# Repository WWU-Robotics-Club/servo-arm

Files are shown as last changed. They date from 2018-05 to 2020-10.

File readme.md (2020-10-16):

Servo robot arm inspired by [Pinaut's project](https://www.youtube.com/watch?v=bLnAJ-mSElE)

pot_control controls the arm via a second arm with potentiometers to measure position like in Pinaut's video.

For assembly instructions see the readme under [instructions](instructions/readme.md).

blueberry_servo_arm is made to work with "keyframes" function of [this fork](https://github.com/CalebJ2/Android-Bluetooth-Remote-Control) of the blueberry remote control app. With the app, keyframe animations can be saved on the phone and played back on the arm.

## Parts list

* Set of laser cut parts made out of 1/8 inch plywood. If that isn't an option they could be cut out of cardboard or foamboard. There are .dwg to .pdf converters that could be used to print plans if autocad isn't available.
* 1x Arduino Uno & USB cable
* 1x V5.0 Sensor Shield (or similar)
* 5x 9g servos (I used 1 SG90 and 4 MG90S servos)
* 5x WH148 Rotary Potentiometers 10K Ohm 15mm shaft
* Misc. 20mm and 10mm jumper wires to extend servo wires and connect potentiometers
* (maybe) 1x USB battery bank to power it. The servos can draw more power than some computer USB ports can supply.

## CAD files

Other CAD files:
autocad files/arm-main.dwg
autocad files/arm-grabber.dwg
autocad files/arm-control.dwg

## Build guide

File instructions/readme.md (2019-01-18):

# Assembly instructions

For glue hot glue works well.

Servo horns are the things you put on servos. Friction fit is probably enough but optionally you can screw them on or use a little hot glue. 

Center each servo before permanently connecting a servo horm. Just turn them to figure out their range and turn it to the center, or use a servo tester or receiver or something to have the servo center itself.

## Step 1

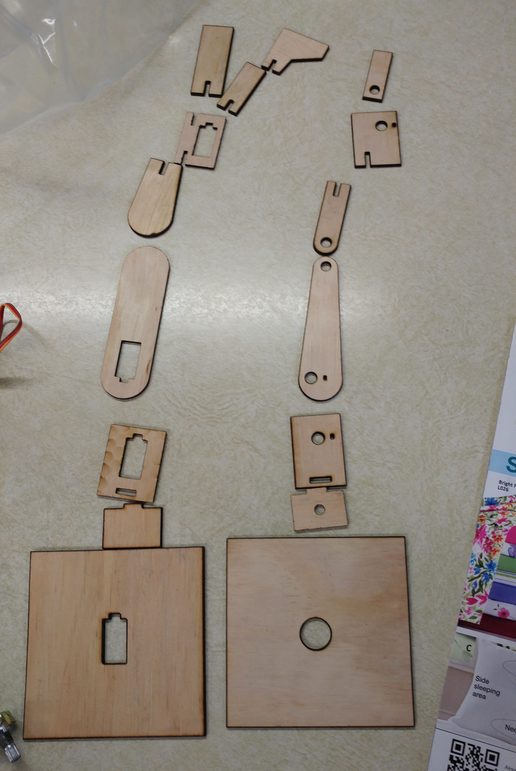
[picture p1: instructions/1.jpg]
Step 1


Take inventory. Left side is the servo arm, right is the control arm.

---

## Step 2

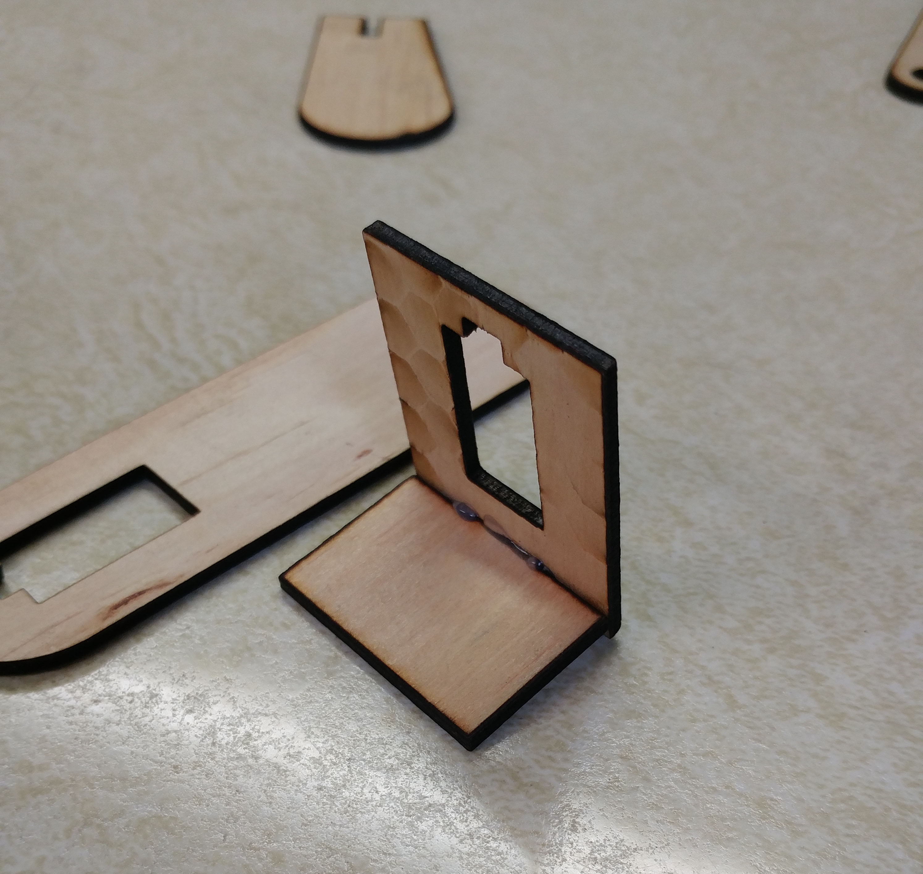
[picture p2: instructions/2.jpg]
Step 2


Servo arm first. Glue these.

---

## Step 3

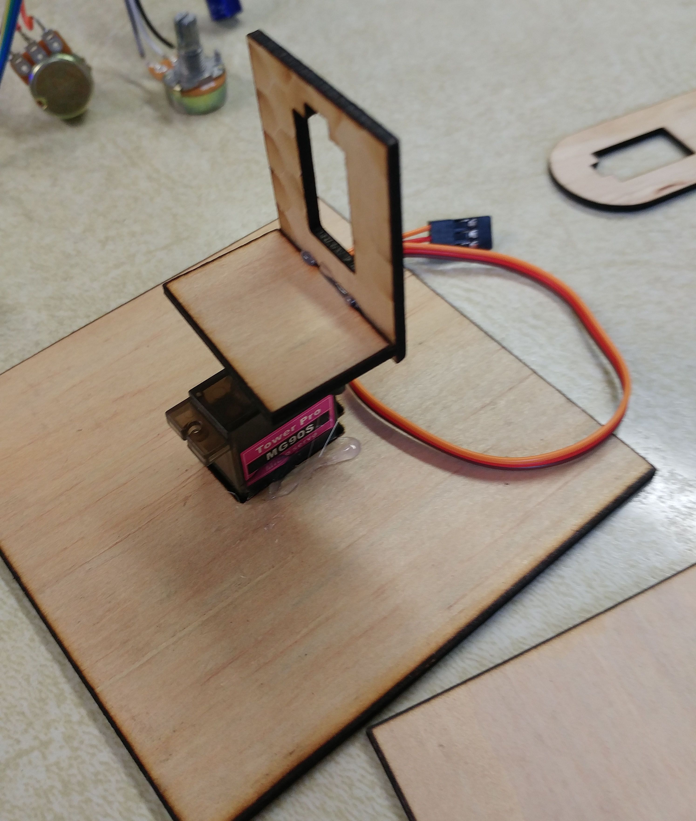
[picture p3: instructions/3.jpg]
Step 3


Glue in the base servo. Put a servo horn on the servo. Glue the part 2 part on top.

---

## Step 4

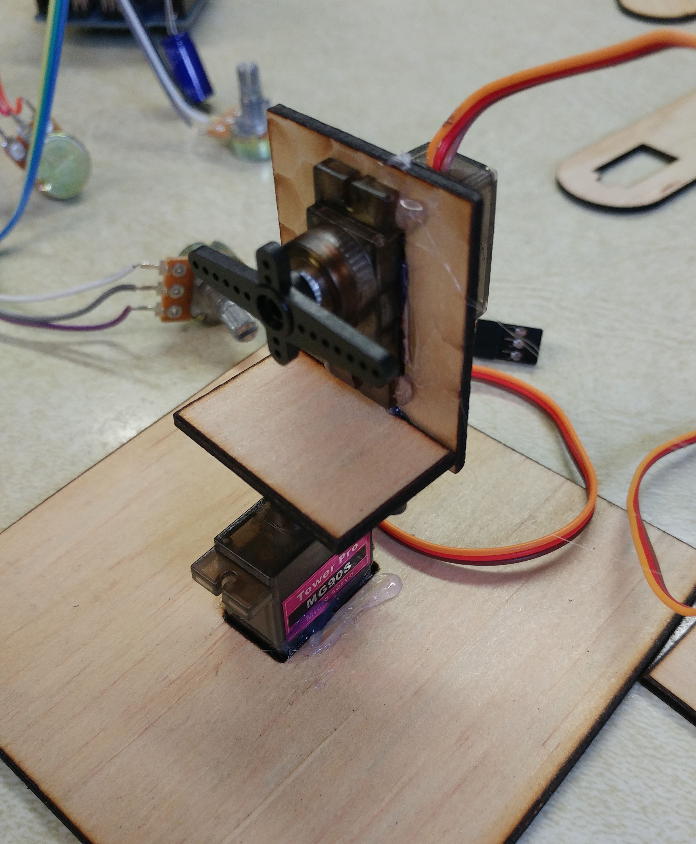
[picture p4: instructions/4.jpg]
Step 4


Glue in the elbow servo with the turning part up.

---

## Step 5

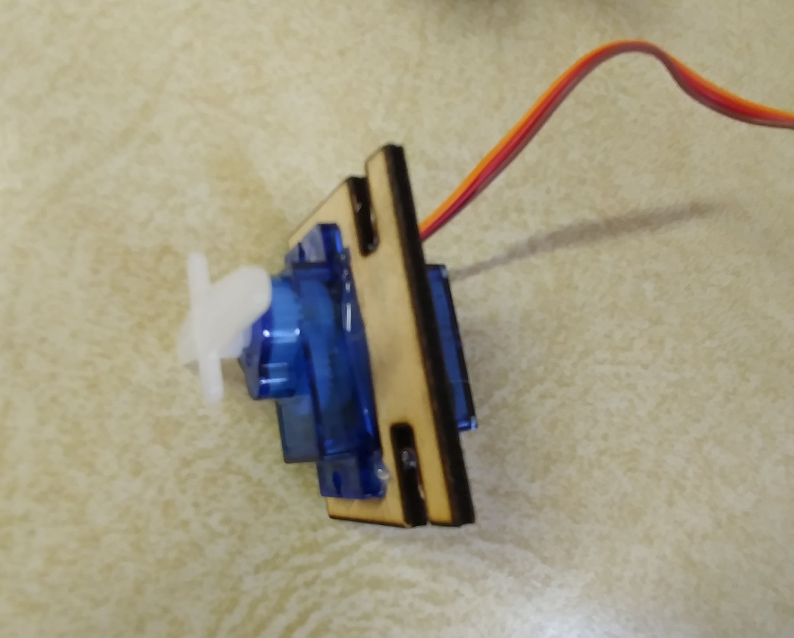
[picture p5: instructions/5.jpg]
Step 5


Carefully glue the grabber servo into the grabber servo mount with the wire facing forward and the slots on the right.

---

## Step 6

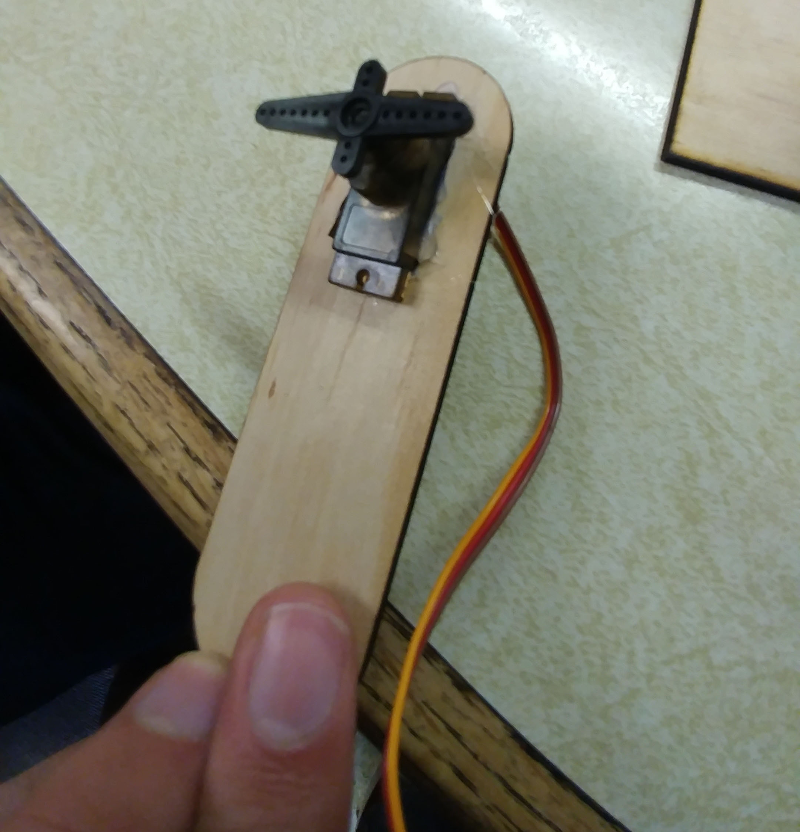
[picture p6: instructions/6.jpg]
Step 6


Glue in the wrist servo with the turning part towards the end.

---

## Step 7

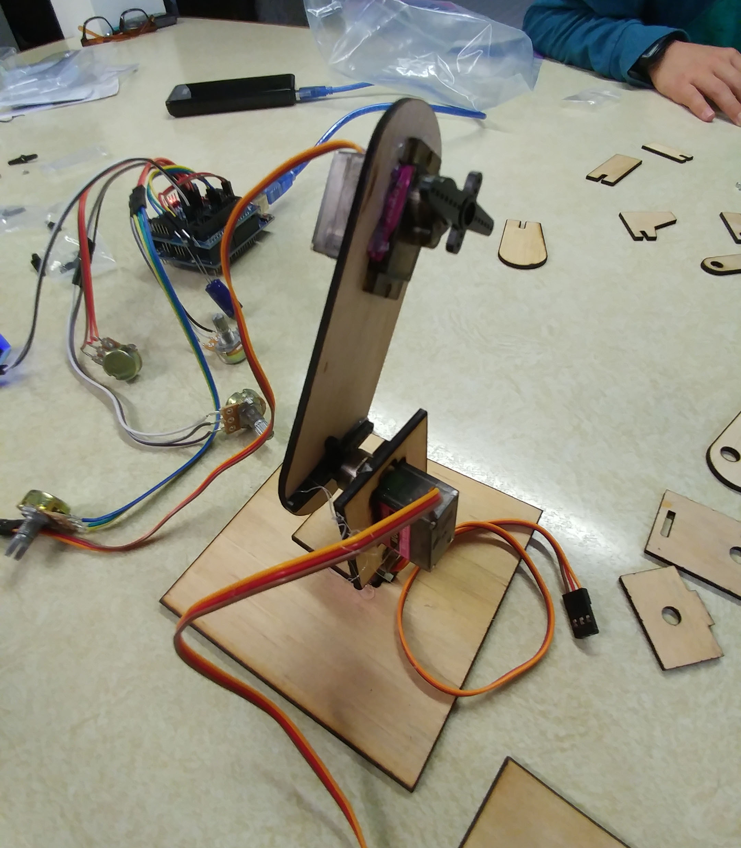
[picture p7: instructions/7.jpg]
Step 7


Glue the arm part onto the elbow servo.

---

## Step 8

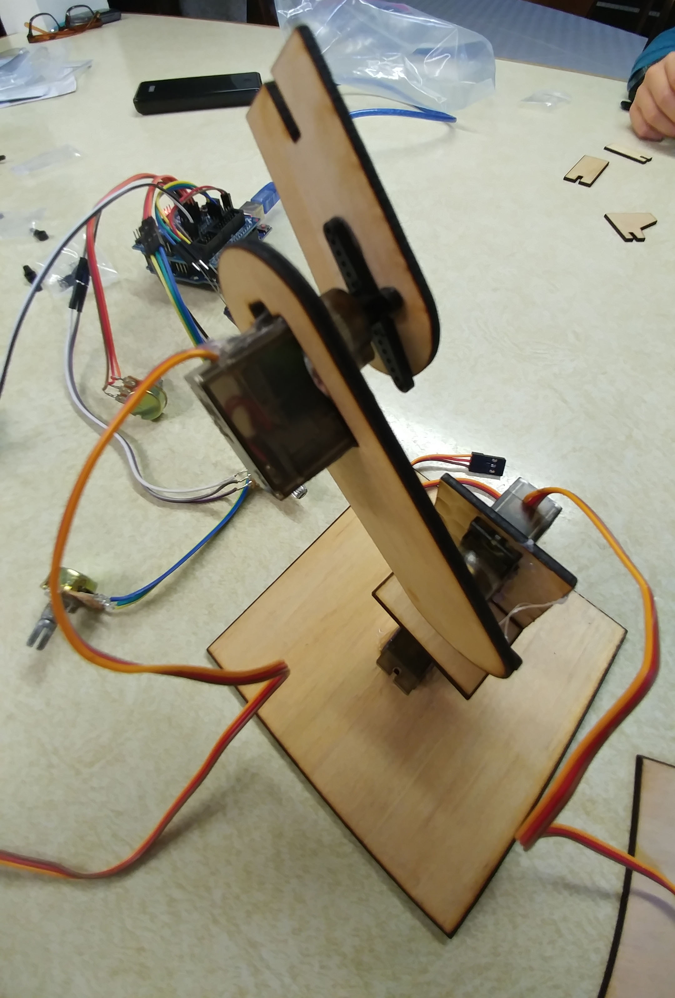
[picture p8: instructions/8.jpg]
Step 8


Glue the first wrist part onto the wrist servo with the 90deg corner on top and the slightly wider angle corner on the bottom.

---

## Step 9

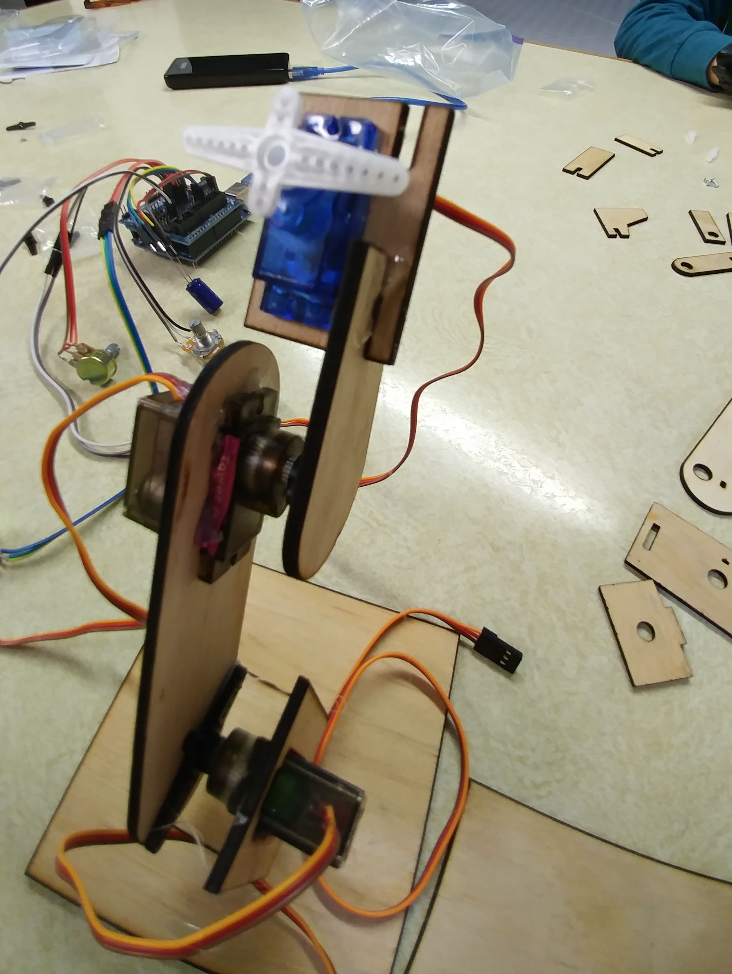
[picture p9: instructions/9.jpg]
Step 9


Slide the grabber servo mount onto the first wrist part. Glue if needed.

---

## Step 10

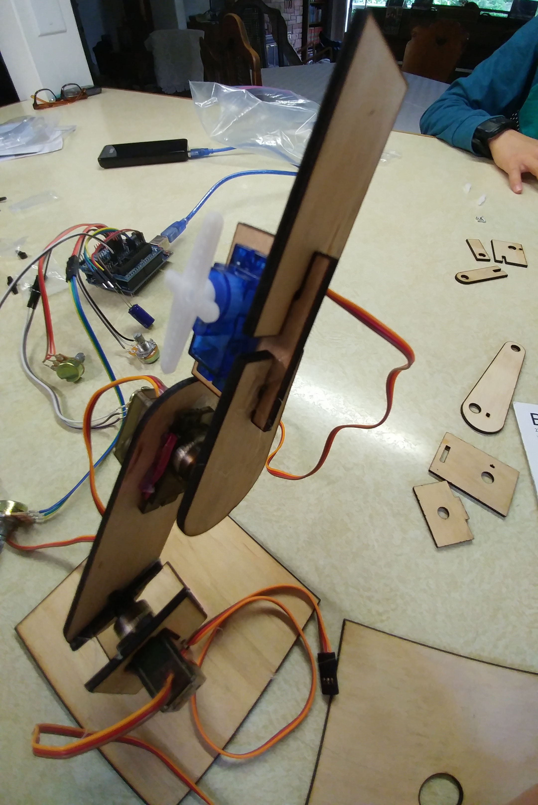
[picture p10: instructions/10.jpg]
Step 10


Slide the grabber "hand" onto the grabber servo holder.

---

## Step 11

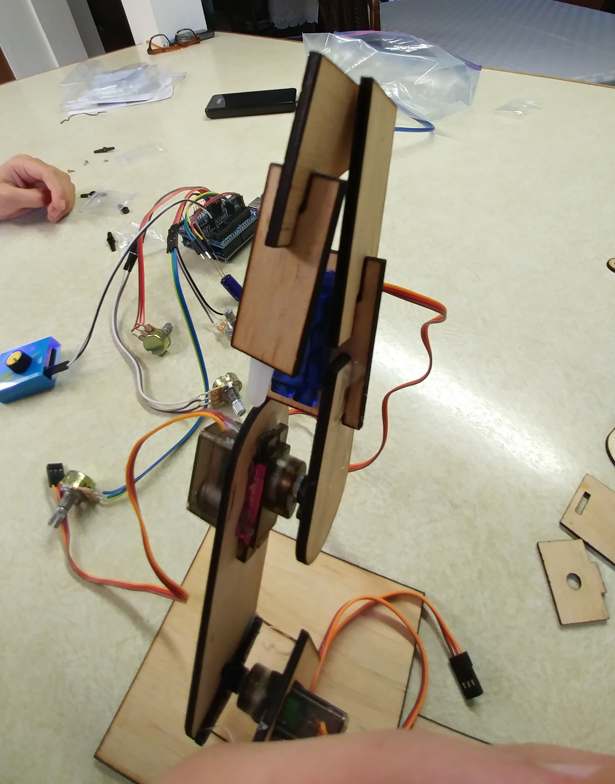
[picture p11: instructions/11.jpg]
Step 11


Slide together the grabber "thumb" pieces and glue them onto the grabber servo. Made sure the end of the hand and thumb line up.

---

## Step 12

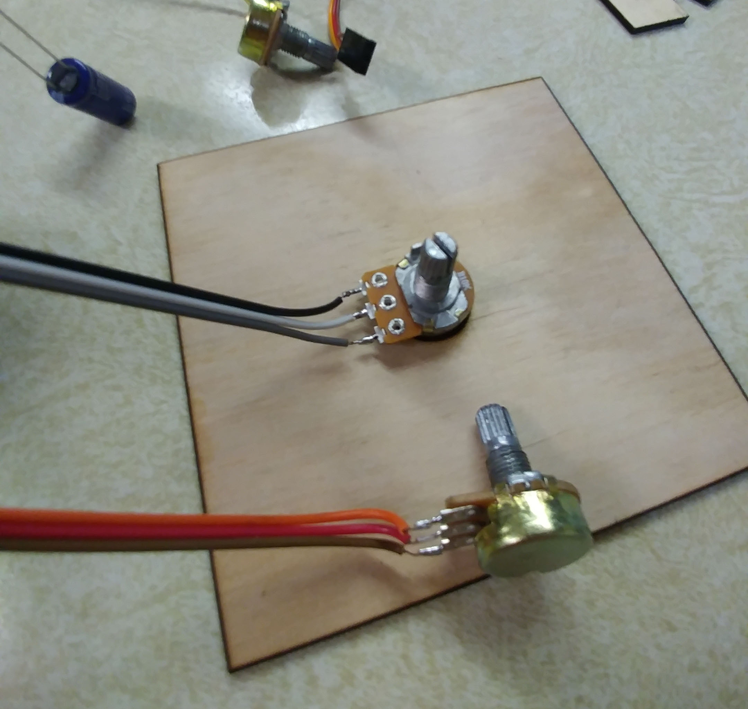
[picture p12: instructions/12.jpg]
Step 12


Next the controller arm. First *solder wires to the potentiometers*. I just stripped one end of some jumper wires and soldered them on. Jumper wires are nice because they are stuck together and are easy to extend by plugging more wires onto the first ones.

Press or glue a potentiometer (aka pot) into the base.

---

## Step 13

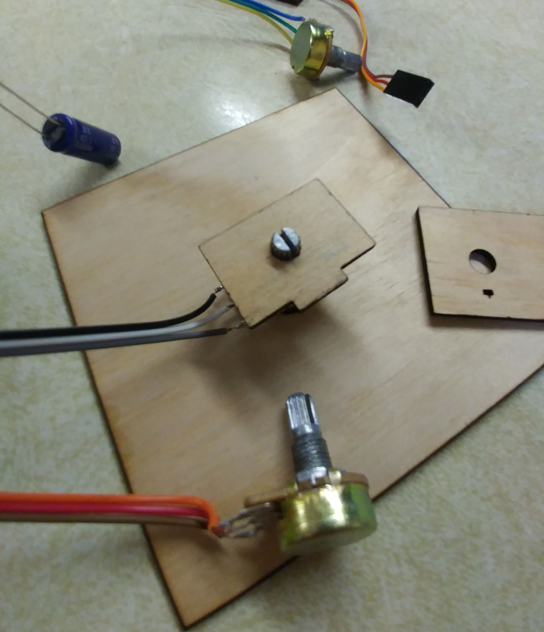
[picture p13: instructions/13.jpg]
Step 13


Center the pot and press the next piece on as shown.

---

## Step 14

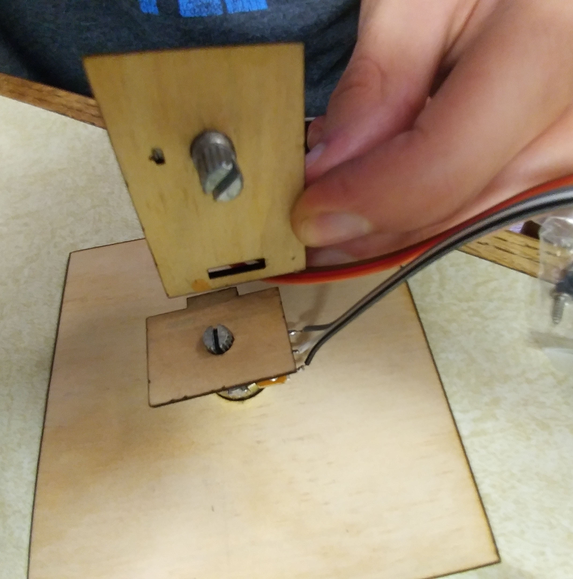
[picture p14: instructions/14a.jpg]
Step 14a

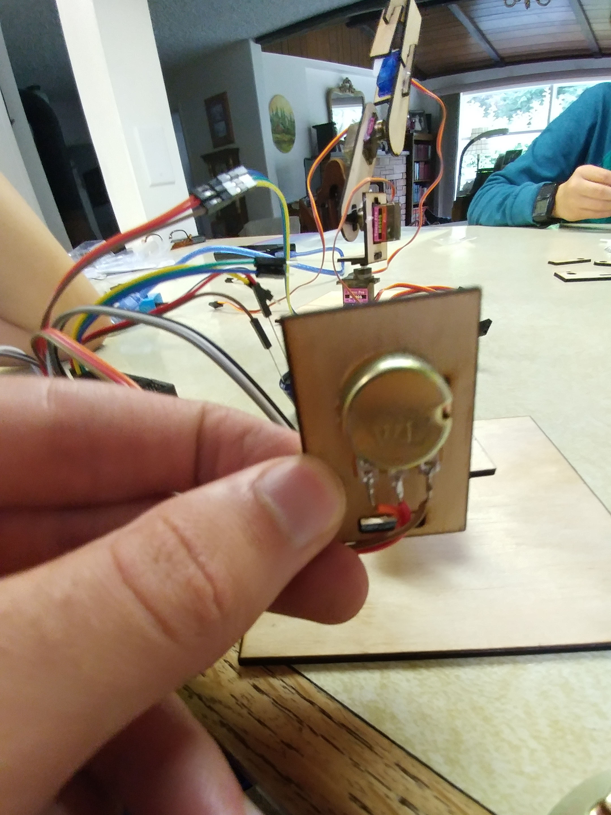
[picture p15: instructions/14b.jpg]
Step 14b


Press the elbow pot on in the orientation shown.

---

## Step 15

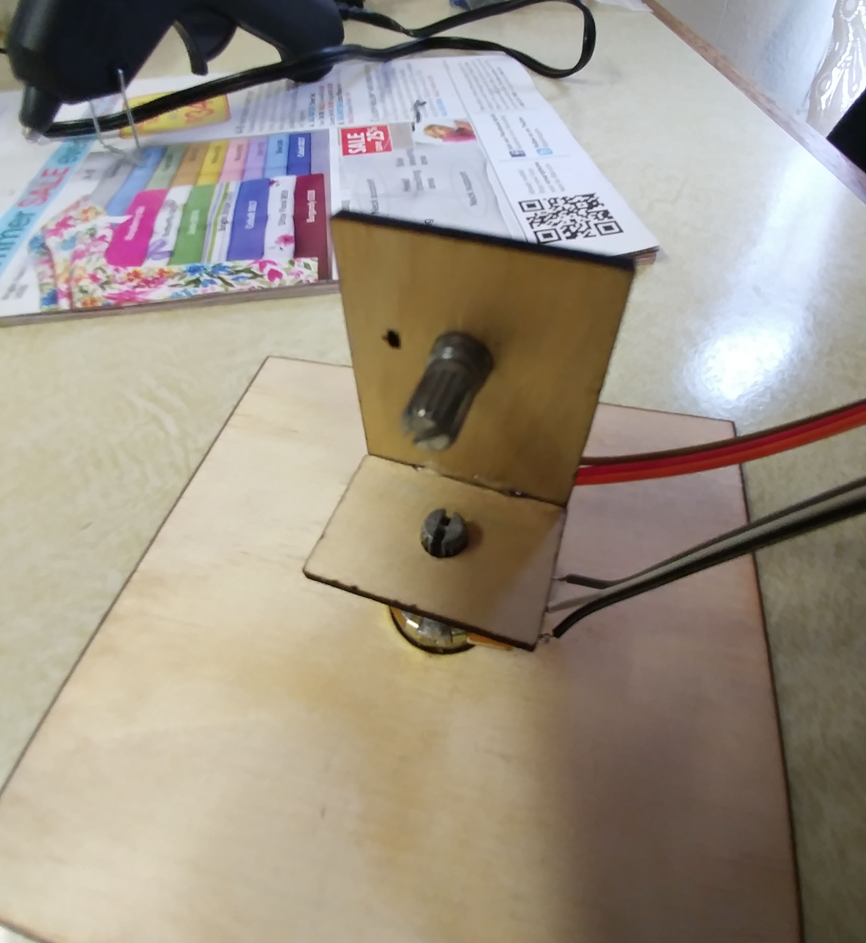
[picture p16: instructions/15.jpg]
Step 15


Glue that to the base.

---

## Step 16

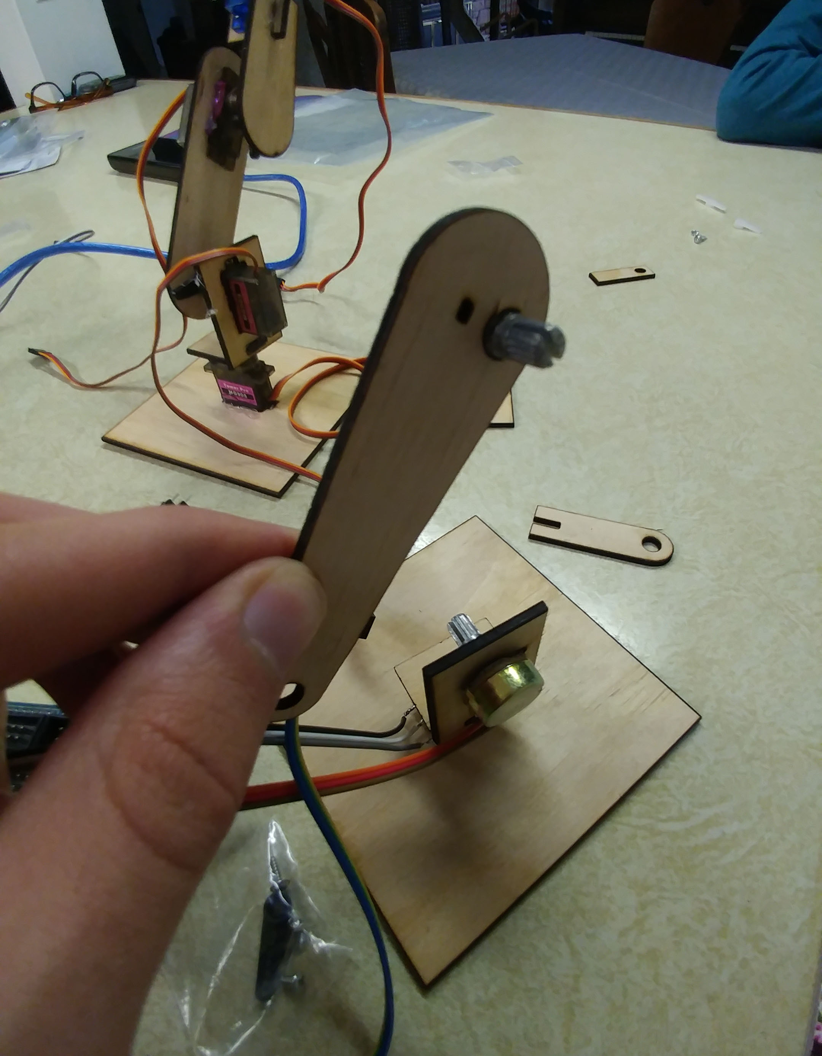
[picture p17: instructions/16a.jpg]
Step 16a

Step 16b

Press the wrist pot onto the arm piece and press the arm onto the elbow pot.

---

## Step 17

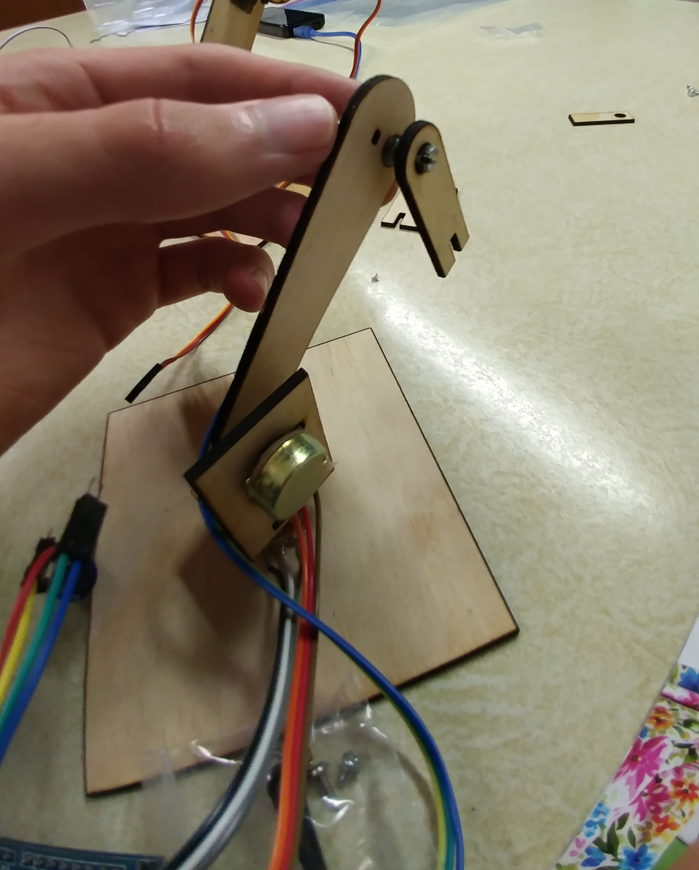
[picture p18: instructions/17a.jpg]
Step 17a

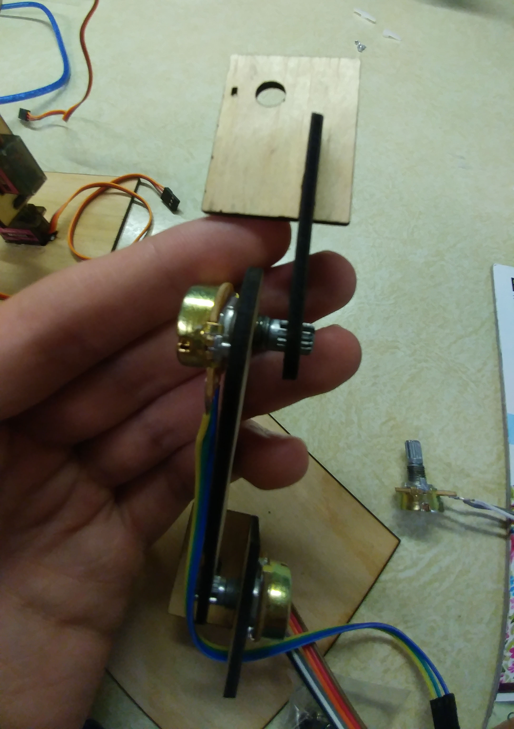
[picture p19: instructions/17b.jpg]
Step 17b


Press the wrist piece onto the wrist pot and slide the grabber pot holder onto the wrist piece.

---

## Step 18

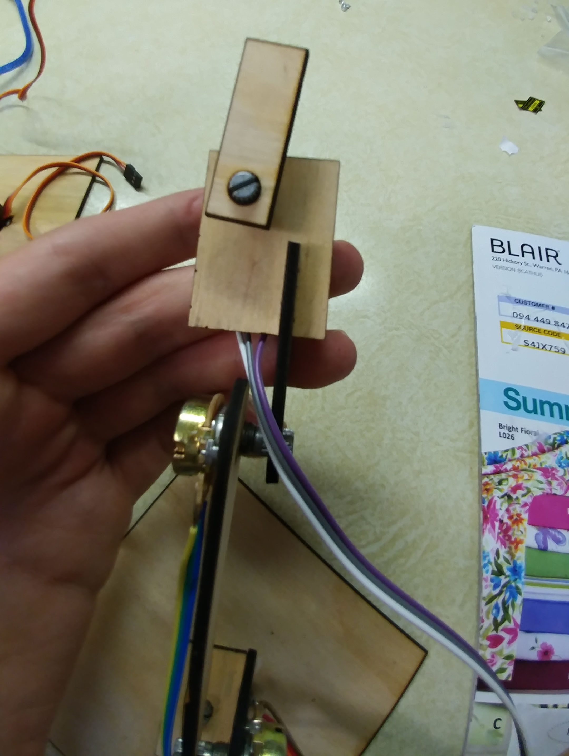
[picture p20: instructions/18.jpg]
Step 18


Press the grabber pot onto the holder piece and press the grabber controller piece onto the pot.

---

## Step 19

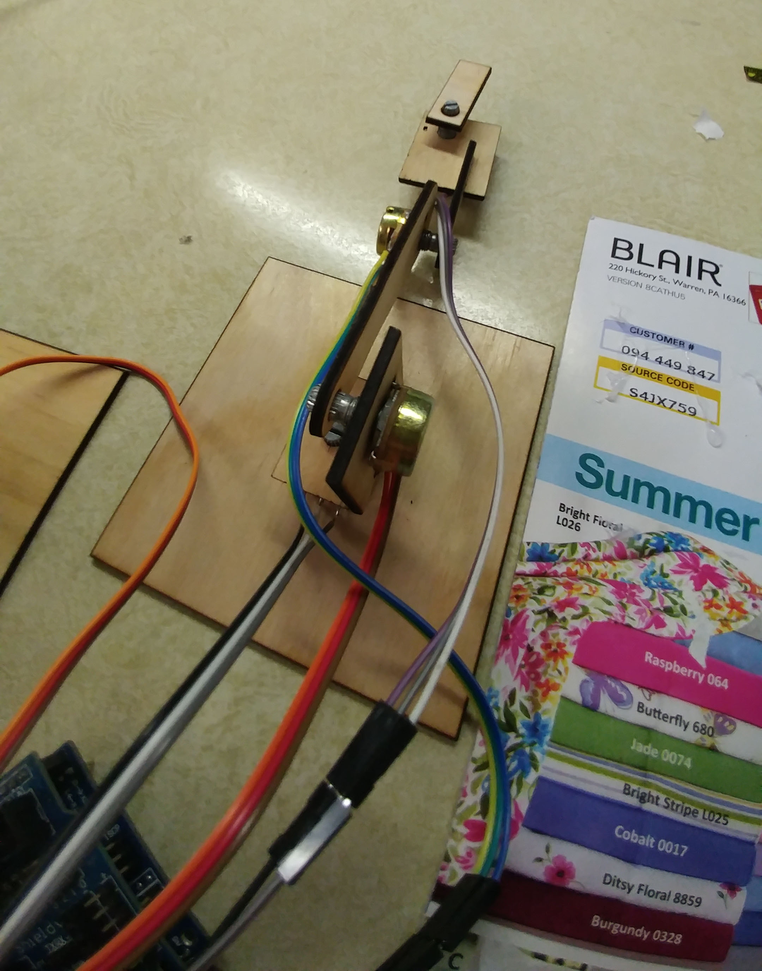
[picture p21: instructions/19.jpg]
Step 19


Add extension wires as needed.

---

## Step 20

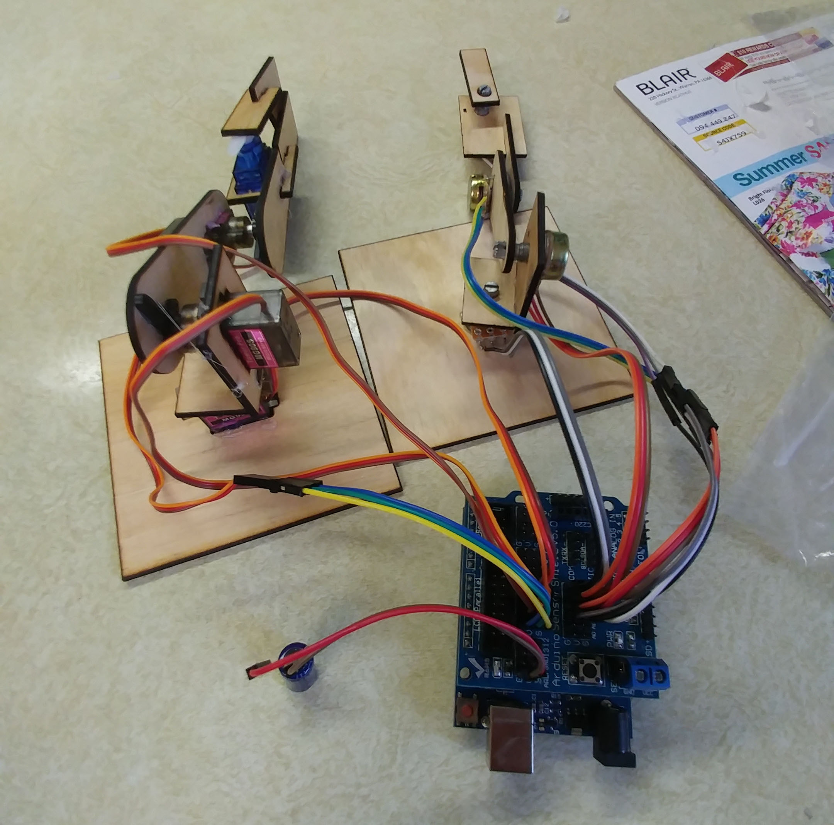
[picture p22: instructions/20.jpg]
Step 20


Connect everything to the arduino. In the example code I have the servos connected to pins 8,9,10,11 starting with the base servo. The potentiometers are connected to a5,a4,a3,a2 starting with the base pot.

It is easiest to use a sensor shield on the arduino. The sensor shield has G, V, and S rows. On the servos, made sure the orange wire goes into the S row of pins. 

The middle pin on the pots should be connected to the "S" row. The other two pins can be connected either way. Switching them reverses the pot.

---

## Step 21

Uploading the program.

The Arduinos we used have a ch340g usb to serial converter for programming the microcontroller. For your computer to recognize the arduino the ch340g driver needs to be installed. I got it from this link and haven't had any problems:  https://kig.re/2014/12/31/how-to-use-arduino-nano-mini-pro-with-CH340G-on-mac-osx-yosemite.html

Plug in the arduino via usb cable.

Open the arduino sketch (pot_control.ino unless you are using a bluetooth module). Under Tools->Board select Arduino/Genuino Uno. Under Tools->Port select a port (probably only one option will be available, otherwise try another if the first doesn't work). Then click Upload (or ctrl+u).

## Step 22

Next we need to calibrate it so the controller and arm move together. The sketch can be modified to do this, or the easier way is to turn on the arm and remove and replace each joint on the controller arm so that it matches the servo arm. If the joint turnes the wrong way, switch the G and V pins of that pot.

Good luck!

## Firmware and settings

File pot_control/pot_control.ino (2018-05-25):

#include <Servo.h>

#define debug false
#define numAxis 4

struct ServoParams {
  int servoPin;
  int potPin;
  int servoMin;
  int servoMax;
  int potMin;
  int potMax;
  Servo servo;
};

// initialize axis parameters
ServoParams axis[] = {
  { // joint 1 / base
    8, // servoPin
    5, // potPin
    5, // servoMin 0-180
    175, // servoMax
    845, // potMin 0-1023
    200, // potMax
    Servo()
  },
  { // joint 2 / shoulder
    9, // servoPin
    4, // potPin
    5, // servoMin 0-180
    175, // servoMax
    20, // potMin 0-1023
    700, // potMax
    Servo()
  },
  { // joint 3 / elbow
    10, // servoPin
    3, // potPin
    5, // servoMin 0-180
    175, // servoMax
    300, // potMin 0-1023
    1020, // potMax
    Servo()
  },
  { // joint 4 / grabber
    11, // servoPin
    2, // potPin
    5, // servoMin 0-180
    175, // servoMax
    1020, // potMin 0-1023
    470, // potMax
    Servo()
  }
};
int val;

void setup() {
  if (debug) {
    Serial.begin(9600);
  } else {
    delay(5000);
    for (int i=0; i < numAxis; i++) {
      axis[i].servo.attach(axis[i].servoPin);
      delay(1000);
    }
  }
}

void loop() {
  if (debug) { // just read pot values
    String tmp = "";
    for (int i=0; i < numAxis; i++) {
      // read the value of the potentiometer (value between 0 and 1023)
      val = analogRead(axis[i].potPin);
      tmp += String(i) + " " + val + ", ";
    }
    Serial.println(tmp);
    delay(15); // wait for the servo to get there
  } else {
    for (int i=0; i < numAxis; i++) {
      // read the value of the potentiometer (value between 0 and 1023)
      val = analogRead(axis[i].potPin);
      // scale it to use it with the servo (value between 0 and 180)
      val = map(val, axis[i].potMin, axis[i].potMax, axis[i].servoMin, axis[i].servoMax);
      // sets the servo position according to the scaled value
      axis[i].servo.write(val);
    }
    delay(15); // wait for the servo to get there
  }
}

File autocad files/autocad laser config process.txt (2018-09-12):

Some notes on using autocad with an epilog laser cutter.

If lines aren't a polyline:
- select line on shape
pedit
- select rest of shape
join

General setup:
- select shape to offset because laser doesn't account for cut width
offset in 0.1, out 0.2
- make new cuts layer under layer properties, select color
- select offsets, go to properties, move layer
- output->plot (or page setup manager the first time)
- set output to engr-epilog-pc3
- plot style epilog.ctb
- drawing orientation portrait
- pick square paper size, eg. 48x48"
- change plot area window, set to same size as paper
- change scaling to appropriate units
- printer is 12 wide, 18 tall
- printer properties for print settings

12in=304.8
18in=457.2mm
48in=1219.2mm

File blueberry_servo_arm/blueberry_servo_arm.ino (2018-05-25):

/*
 * Title:        Bluetooth Remote Control
 * Description:  This program is intented to work with a connected
 *               Bluetooth dongle to the robot and an Android phone
 *               running Blueberry application
 * Author:       Karl Kangur <karl.kangur@gmail.com>
 * Modified by:  CalebJ2
 * Version:      1.0
 * Website:      github
 */
#include <Servo.h>

// how many servos are attached
#define numChannels 4

Servo servos[numChannels];
int servoPins[] = {8,9,10,11};
int* tmpArr;
// keyframe inputs. Default everything to 90
int* currentFrame = new int[7]; // transition from
int* midFrame = new int[7]; // currently at
int* nextFrame = new int[7]; // transition to
unsigned long frameStart = 0; // time

char serialData[32];
byte error = 0;
unsigned long lastRxTime;
unsigned long lastServoTime;
unsigned long currentTime;
boolean connected; //has communicated with phone within last second? This is mostly unused.

void setup()
{
  // the bluetooth dongle communicates at 9600 baud only
  Serial.begin(115200);
  lastRxTime = millis();
  
  for (int i=0; i < numChannels; i++) {
    servos[i].attach(servoPins[i]);
  }
  // default frames to 90
  for (int i=0; i < 7; i++) {
    currentFrame[i] = 90;
    midFrame[i] = 90;
    nextFrame[i] = 90;
  }
}

void loop()
{
  if(millis()-lastRxTime > 1500 && connected == true){//if this hasn't heard from phone for 1.5 seconds
    //Serial.println("reset due to timeout ");
    //connected = false;
    //reset();
  }
  if(Serial.available() > 0)
  {
    // clear timeout
    connected = true;
    lastRxTime = millis();

    Serial.readBytesUntil('\n', serialData, 31);
    switch(serialData[0])
    {
    case 0: //basically the blueberry ping command
      Serial.println(0);
      break;
    case 'k':
      // set up transition from current position to recieved frame
      tmpArr = new int[7];
      if(parseCommand(serialData, tmpArr, 7)) {
        // start next frame. midFrame should be close to next frame, so just transition from it
        // to avoid jumps. Delete currentFrame and shift everything else down to avoid memory leaks.
        midFrame[0] = nextFrame[0];
        delete currentFrame;
        currentFrame = midFrame;
        midFrame = nextFrame;
        nextFrame = tmpArr;
        frameStart = millis();
        Serial.println('0'); // confirm reception
      } else {
        delete tmpArr;
        Serial.print("Error while parsing command. ");
        Serial.println(String(serialData));
      }
      break;
    case 'r':
      reset();
      Serial.println("Robot reset");
      break;
    default:
      // inform user of non existing command
      Serial.print("Command not recognised. ");
      Serial.println(String(serialData));
    }

    // clear serialData array
    memset(serialData, 0, sizeof(serialData));
  }
  //k,5000,10,10,10,10,0,0
  //String tmp = "";
  int timeIntoFrame = constrain(millis() - frameStart, 0, currentFrame[0]);
  // like percent except out of 1000 to minimize integer rounding errors
  // (frame delay - timeElapsed) / frame delay * 1000
  int scalar = ((long)currentFrame[0] - (long)timeIntoFrame) * (long)1000 / (long)currentFrame[0];
  midFrame[0] = currentFrame[0] - timeIntoFrame;
  //tmp += "millis " + String(millis()) + ", time " + String(timeIntoFrame) + ", ft0 " + String(currentFrame[0]) + ", scalar " + String(scalar);
  for (int i = 1; i < numChannels+1; i++) {
    midFrame[i] = (long)currentFrame[i] * scalar / 1000 + (long)nextFrame[i] * (1000 - scalar) / 1000;
    midFrame[i] = constrain(midFrame[i], 6, 174);
    //tmp += "; i " + String(i) + ", val " + String(midFrame[i]);
  }
  for (int i = 0; i < numChannels; i++) {
    servos[i].write(midFrame[i+1]);
  }
  //Serial.println(tmp);
  //delay(50);
}

void reset()
{
  for (int i=1; i <= 4; i++) {
    //servos[i-1].write(90);
  }
}

/**
 * This function makes ints out of the received serial data, the 2 first
 * characters are not counted as they consist of the command character and
 * a comma separating the first variable.
 *
 * @params command The whole serial data received as an address
 * @params returnValues The array where the return values go as an address
 * @params returnNumber The number of values to set inside the returnValues variable
 */
boolean parseCommand(char* command, int* returnValues, byte returnNumber)
{
  // parsing state machine
  byte i = 1, j = 0, sign = 0, ch = 0, number;
  int temp = 0;
  while(i++)
  {
    switch(*(command + i))
    {
    case '\0':
    case ',':
      // set return value
      if(ch != 0)
      {
        returnValues[j++] = sign?-temp:temp;
        sign = 0;
        temp = 0;
        ch = 0;
      }
      else
      {
        return false;
      }
      break;
    case '-':
      sign = 1;
      break;
    default:
      // convert string to int
      number = *(command + i) - '0';
      if(number < 0 || number > 9)
      {
        return false;
      }
      temp = temp * 10 + number;
      ch++;
    }

    // enough return values have been set
    if(j == returnNumber)
    {
      return true;
    }
    // end of command reached
    else if(*(command + i) == '\0')
    {
      return false;
    }
  }
}
